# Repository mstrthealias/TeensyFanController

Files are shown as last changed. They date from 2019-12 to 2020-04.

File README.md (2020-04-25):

# Teensy Fan Controller

*Documentation: [https://mstrthealias.gitbook.io/teensy-fan-controller/][7]*

A PC fan controller with temperature sensor input, for **[Teensy](https://www.pjrc.com/teensy/index.html) 3.x** USB Development Board(s).

Supports up to 6 fans (4pin/PWM), and up to 5 temperature sensors. Each fan may individually operate in PID, temperature-percent table, or fixed-percent control modes. Configuration is saved onto the device, and software is not required other than to configure the controller.

## Documentation

The project is **documented using Gitbook**, and accessible at **[https://mstrthealias.gitbook.io/teensy-fan-controller/][7]**.

## Releases

- v0.1.0
  - [Firmware (Teensy 3.2, 3.5)](https://github.com/mstrthealias/TeensyFanController/releases/tag/v0.1.0)
  - [Configuration UI (Windows 10)](https://github.com/mstrthealias/TFC-ui/releases/tag/v0.1.0)

## Hardware

* [Prototype - Simple PCB][4]: requires PCB fabrication (gerber files provided) and through-hole soldering
* [Prototype - Breadboard][2]: breadboard example with a single fan/single sensor
* [Prototype - Hand-made (Schmart Board based)][3]: uses over-the-shelf components (OK for single fan/single sensor builds)

## Software

### Qt UI

[Teensy Fan Controller UI (Qt5)](https://github.com/mstrthealias/TFC-ui): provides a user interface to configure or monitor the fan controller (only needed for initial configuration).

### Linux Kernel module (hwmon)

[Fork of liquidtux](https://github.com/mstrthealias/liquidtux): Linux kernel module for reading temperatures and fan RPMs using *lm-sensors* or *psensor*.  Tested on Ubuntu 18.04.

## Simple 001 PCB

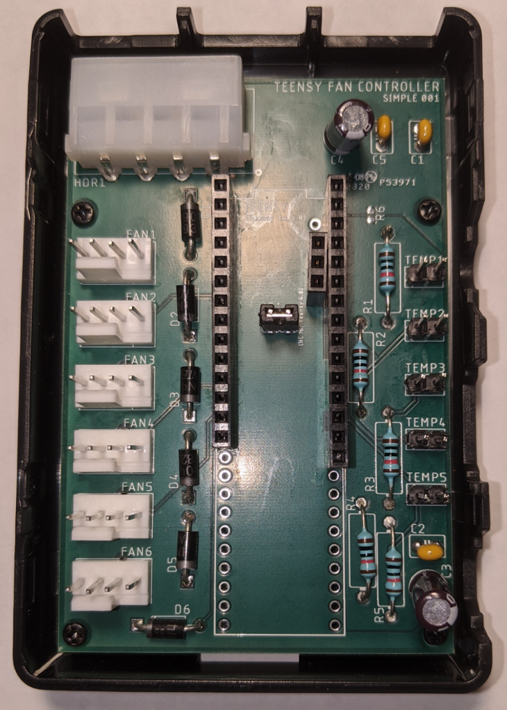
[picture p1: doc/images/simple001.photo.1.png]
Simple 001 PCB


## [Credits](https://mstrthealias.gitbook.io/teensy-fan-controller/credits)

Icons made by [Freepik](https://www.flaticon.com/authors/freepik) from [www.flaticon.com](https://www.flaticon.com/):

* ui_qt5/images/log.svg
* ui_qt5/images/worldwide.svg

[2]: https://mstrthealias.gitbook.io/teensy-fan-controller/hardware/breadboard
[3]: https://mstrthealias.gitbook.io/teensy-fan-controller/hardware/prototype
[4]: https://mstrthealias.gitbook.io/teensy-fan-controller/hardware/simple-pcb
[5]: Hardware/
[6]: https://mstrthealias.gitbook.io/teensy-fan-controller/demo/router-cooling-demo
[7]: https://mstrthealias.gitbook.io/teensy-fan-controller/

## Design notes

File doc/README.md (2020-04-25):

# Teensy Fan Controller

A PC fan controller with temperature sensor input, for **[Teensy](https://www.pjrc.com/teensy/index.html) 3.x** USB Development Board\(s\).

Supports up to 6 fans \(4pin/PWM\), and up to 5 temperature sensors \(thermistors\). Each fan may individually operate in PID, temperature-percent table, or fixed-percent control modes.

Designed to control radiator fans on a PC water cooling loop \(to maintain supply water temperature\), but may be configured for other purposes \(for example, see [Demo/Router Cooling Demo](demo/router-cooling-demo.md)\).

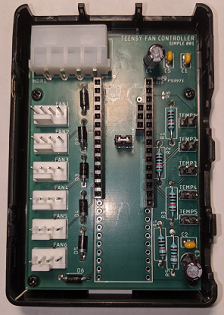
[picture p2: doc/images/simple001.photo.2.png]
Simple 001 PCB in a Raspberry Pi 3 case


## Releases

- v0.1.0
  - [Firmware (Teensy 3.2, 3.5)](https://github.com/mstrthealias/TeensyFanController/releases/tag/v0.1.0)
  - [Configuration UI (Windows 10)](https://github.com/mstrthealias/TFC-ui/releases/tag/v0.1.0)

## Hardware

The following hardware has been used with Teensy Fan Controller:

* [Prototype - Simple PCB](hardware/simple-pcb.md): requires PCB fabrication \(gerber files provided\) and through-hole soldering
* [Breadboard](hardware/breadboard.md): breadboard example with a single fan/single sensor
* [Prototype - Hand-made \(Schmart Board based\)](hardware/prototype.md): uses over-the-shelf components

Related files are available in the [TeensyFanController/Hardware](https://github.com/mstrthealias/TeensyFanController/tree/master/Hardware) folder.

### Hardware Interface

The Teensy Micro USB port is used to configure and monitor the fan controller.

{% hint style="info" %}
It is possible to connect the Micro USB port to an internal motherboard USB 1.1/2.0 header, by making a custom cable, or purchasing a _Micro USB 5pin Male to 1x 5Pin Female 0.1" USB Header PCB Motherboard Cable_.
{% endhint %}

## Software

### Qt UI

[Teensy Fan Controller UI \(Qt5\)](https://github.com/mstrthealias/TFC-ui): provides a user interface to configure or monitor the fan controller (only needed for initial configuration).

### Linux Kernel module \(hwmon\)

[Fork of liquidtux](https://github.com/mstrthealias/liquidtux): Linux kernel module for reading temperatures and fan RPMs using *lm-sensors* or *psensor*.  Tested on Ubuntu 18.04.

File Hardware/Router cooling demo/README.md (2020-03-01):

# Teensy Fan Controller - Router Cooling Demo

The controller is configured to cool a temperature sensor (placed between a desk router and switch) to a specific temperature.

A single PWM fan and single sensor is connected to a Teensy 3.2 using a breadboard.

## Hardware Requirements

1. One Breadboard, or a Teensy Fan Controller board (fe. Simple 001)
1. One Teensy 3.x with headers (previously *flashed with Teensy Fan Controller*)
1. A Micro USB cable
1. One 10k thermistor (fe. [Adafruit 10K Precision Epoxy Thermistor - 3950 NTC][1])
1. One 10k Ohm resistor (ideally 1% or better accuracy)
1. One standard/rectifier diode (fe. 1N4004)
1. One 12v power supply (up to 15V should be OK)
1. One PWM PC fan (80mm, 120mm, 140mm)
1. Wires

[1]: https://www.adafruit.com/product/372

## Hardware Setup

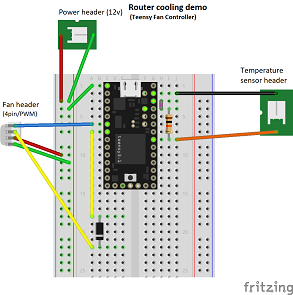
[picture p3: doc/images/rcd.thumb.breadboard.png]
Breadboard wiring diagram
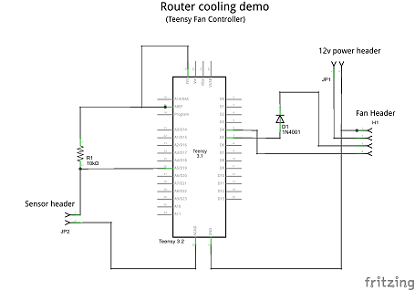
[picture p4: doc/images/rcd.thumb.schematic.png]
Schematic
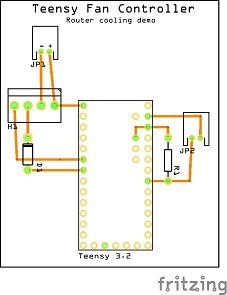
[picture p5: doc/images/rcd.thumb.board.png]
Board example
  

Steps to set up a breadboard with a Teensy 3.2, a single fan, a single temperature sensor, and a 12v power supply:

1. Place the **Teensy** into the top end of the breadboard (Teensy GND on breadboard row 1)
1. Place a **10k Ohm resistor** between **Teensy AREF** (breadboard **I4**) and **Teensy A5** (breadboard **I8**)
1. Place a **diode** with anode at **Teensy D5** (breadboard **A6**) and cathode at breadboard **row 22** (use a wire if needed)
1. Connect **Teensy GND** (breadboard **A1**) to the **GND bus** on the **left side** of the breadboard
1. Connect **Teensy AREF** (breadboard **H3**) to **Teensy V3.3** (breadboard **H4**)
1. Connect fan (4pin PWM):
   1. Connect **fan pin 1 (GND)** to the **GND bus** on the **left side** of the breadboard
   1. Connect **fan pin 2 (12V)** to the **PWR bus** on the **left side** of the breadboard
   1. Connect **fan pin 3 (RPM)** to breadboard **row 22** (cathode side of diode)
   1. Connect **fan pin 4 (PWM)** to **Teensy D4** (breadboard **A6**)
1. Connect thermistor:
   1. Connect **thermistor pin 1** to **Teensy A5** (breadboard **J8**)
   1. Connect **thermistor pin 2** to **Teensy AGND** (breadboard **J2**)
1. Connect 12v power supply the left breadboard bus:
   1. Connect **power supply GND** to the **GND bus** on the **left side** of the breadboard
   1. Connect **power supply +12V** to the **PWR bus** on the **left side** of the breadboard

### Sensor and fan placement

TODO 

<div class="ctbl-wrapper">
<table>
<tbody>
<tr>
<td>

* The temperature sensor is placed between the cases of a router stacked on top of a switch
* The fan is pointed at the router/switch

</td>
<td align="right">

Router cooling demo - sensor/fan setup

</td>
</tr>
</tbody>
</table>
</div>

## Software Setup

Note the Teensy connections made in the previous section:

Signal | Teensy Pin
------ | ---------
Fan 1 RPM pin | D5 (pin 5)
Fan 1 PWM pin | D4 (pin 4)
Thermistor pin 1 | A5 (pin 19)

Configure the software using the information given above:

<div class="ctbl-wrapper">
<table>
<tbody>
<tr>
<td>

1. Connect the **Micro USB cable** to the **Teensy 3.x**
1. Launch **Teensy Fan Controller UI**
1. Select **Menu** > **Hardware Setup**
1. Enter the following:

    Field | Value
    ----- | -----:
    Water Supply Temp Sensor: Pin | **19**
    Water Return Temp Sensor: Pin | 0
    Case Temp Sensor: Pin | 0
    Aux1 Temp Sensor: Pin | 0
    Aux2 Temp Sensor: Pin | 0
    Fan 1: PWM Pin | **4**
    Fan 1: RPM Pin | **5**
    Fan 2: PWM Pin | 0
    Fan 2: RPM Pin | 0
    Fan 3: PWM Pin | 0
    Fan 3: RPM Pin | 0
    Fan 4: PWM Pin | 0
    Fan 4: RPM Pin | 0
    Fan 5: PWM Pin | 0
    Fan 5: RPM Pin | 0
    Fan 6: PWM Pin | 0
    Fan 6: RPM Pin | 0

1. Click **Save**
1. Click the **back arrow** on the top-left

</td>
<td align="right">

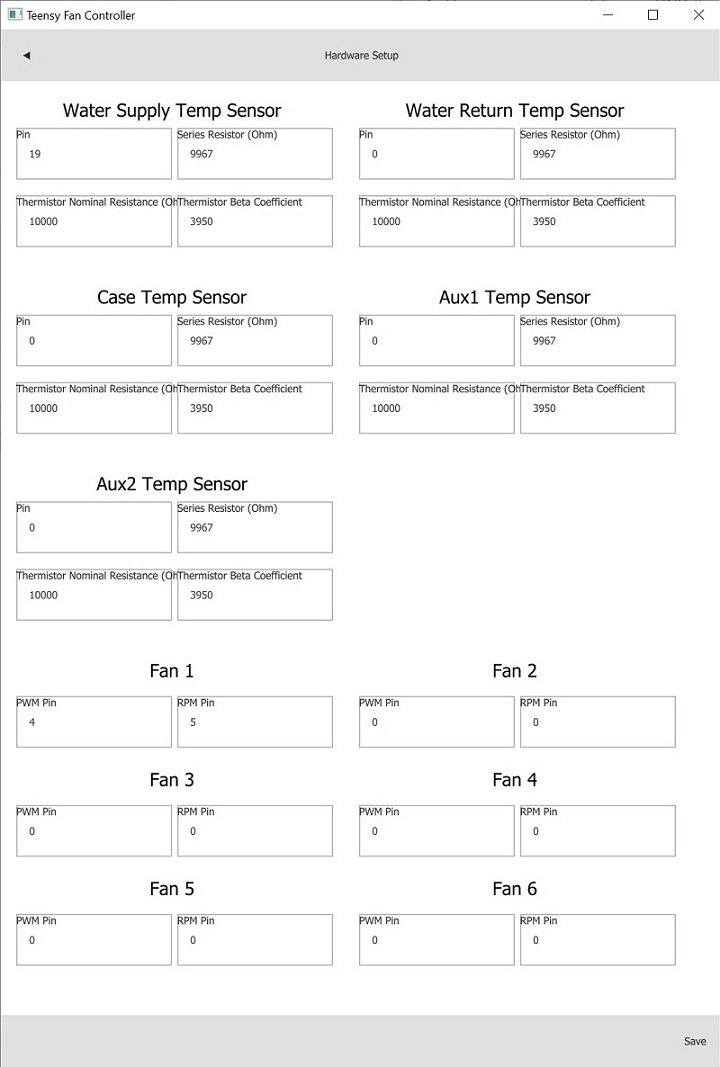
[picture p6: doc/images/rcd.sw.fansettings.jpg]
Router cooling demo - fan settings


</td>
</tr>
</tbody>
</table>
</div>

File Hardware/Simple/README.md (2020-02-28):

# Teensy Fan Controller - PCB Simple001

The initial, untested, simple Teensy Fan Controller PCB.

Designed to fit in a [Raspberry Pi 3 case][1].

## Instructions

TODO

## Notes

After this revision has been tested, a 2nd revision--Simple002--will be published, possibly removing features such as the AGND-GND bridge and V3.3-AREF jumper.

- The jumper in the middle ties v3.3 to ADC reference voltage

TODO

## Features

TODO

- Supports Teensy 3.x, and Teensy 4.0
- Standard 4pin Molex PC power connector
- Fits in a [Raspberry Pi 3 case][1]
- 6 fans
- 5 temperature sensors

## Paths

| Path | Description |
|---|---|
| [datasheets/][2] | Part datasheets
| [simple001/EAGLE/][3] | EAGLE library, schematic, and board (Simple001)
| [simple001/gerbers.zip][4] | Gerber files for PCB fabrication (Simple001)
| [simple001/parts.csv][5] | Part order list (Simple001)
| [simple001/partslist.txt][6] | Modified EAGLE partlist.txt export (Simple001)
| [simple001/schematic.pdf][7] | Schematic print-out PDF (Simple001)
| [simple001/freeDFM.pdf][8] | freeDFM multi-layer PDF output results (Simple001)

[1]: https://www.microcenter.com/product/614861/micro-connectors-plastic-raspberry-pi-3-model-b-case-kit
[2]: datasheets/
[3]: simple001/EAGLE/
[4]: simple001/gerbers.zip
[5]: simple001/parts.csv
[6]: simple001/partslist.txt
[7]: simple001/schematic.pdf
[8]: simple001/freeDFM.pdf

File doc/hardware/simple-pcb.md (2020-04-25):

# Simple PCB

The initial Teensy Fan Controller PCB, designed to fit in a [Raspberry Pi 3 case](https://www.microcenter.com/product/614861/micro-connectors-plastic-raspberry-pi-3-model-b-case-kit):

Simple 001 PCB in a Raspberry Pi 3 case

{% hint style="info" %}
[Simple002 design files](https://github.com/mstrthealias/TeensyFanController/blob/master/Hardware/Simple/simple002) are available, but untested.
{% endhint %}

## Build Instructions

* Order PCB fabrication using the provided [Gerber files](https://github.com/mstrthealias/TeensyFanController/blob/master/Hardware/Simple/simple001/gerbers.zip) \(fe. 4pcb 33each\)
* Order parts using provided [bill-of-materials](https://github.com/mstrthealias/TeensyFanController/blob/master/Hardware/Simple/simple001/parts.csv)
* Solder parts onto PCB, guided by the provided [parts list](https://github.com/mstrthealias/TeensyFanController/blob/master/Hardware/Simple/simple001/partslist.txt)

{% hint style="info" %}
_Simple 001_ board mount holes do not exactly fit the enclosure. Perform these steps to fit the PCB in the enclosure:

* Increase board mount hole size using a _7/64"_ drill bit
* Remove the in-board portion of the enclosure stand-offs \(keeping the majority of each stand-off\)
{% endhint %}

## Features

* Supports Teensy 3.x
* Standard 4pin Molex PC power connector
* Fits in a [Raspberry Pi 3 case](https://www.microcenter.com/product/614861/micro-connectors-plastic-raspberry-pi-3-model-b-case-kit)
* 6 fans
* 5 temperature sensors

{% hint style="warning" %}
_Simple 001_ **fan 6** control is not functional when used with a Teensy 3.2.
{% endhint %}

## Notes

* The jumper in the middle \(JP1\) ties v3.3 to ADC reference voltage
* The AGND-GND bridge \(R6\) is left open

{% hint style="info" %}
A 2nd revision--Simple002--will be published, removing the AGND-GND bridge and the V3.3-AREF jumper.
{% endhint %}

## Paths

| Path | Description |
| :--- | :--- |
| [datasheets/](https://github.com/mstrthealias/TeensyFanController/tree/master/Hardware/Simple/datasheets) | Part datasheets |
| [EAGLE/](https://github.com/mstrthealias/TeensyFanController/tree/master/Hardware/Simple/EAGLE) | EAGLE library, schematic, and board \(_Simple 002_\) |
| [simple001/gerbers.zip](https://github.com/mstrthealias/TeensyFanController/tree/0ceefdbffbd5efc627939be4be3313a873193821/Hardware/Simple/simple001/gerbers.zip) | Gerber files for PCB fabrication \(_Simple 001_\) |
| [simple001/parts.csv](https://github.com/mstrthealias/TeensyFanController/tree/0ceefdbffbd5efc627939be4be3313a873193821/Hardware/Simple/simple001/parts.csv) | Part order list \(_Simple 001_\) |
| [simple001/partslist.txt](https://github.com/mstrthealias/TeensyFanController/tree/0ceefdbffbd5efc627939be4be3313a873193821/Hardware/Simple/simple001/partslist.txt) | Modified EAGLE partlist.txt export \(_Simple 001_\) |
| [simple001/schematic.pdf](https://github.com/mstrthealias/TeensyFanController/tree/0ceefdbffbd5efc627939be4be3313a873193821/Hardware/Simple/simple001/schematic.pdf) | Schematic print-out PDF \(_Simple 001_\) |
| [simple001/freeDFM.pdf](https://github.com/mstrthealias/TeensyFanController/tree/0ceefdbffbd5efc627939be4be3313a873193821/Hardware/Simple/simple001/freeDFM.pdf) | freeDFM multi-layer PDF output results \(_Simple 001_\) |

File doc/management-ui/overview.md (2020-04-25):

# Overview

A Qt 5 based application to configure or monitor a Teensy Fan Controller.

{% hint style="info" %}
After clicking Save, the configuration is saved onto the hardware, and is restored after power-loss \(without using the _Management UI_\).
{% endhint %}

## Getting Started

The application attempts to connect when launched:

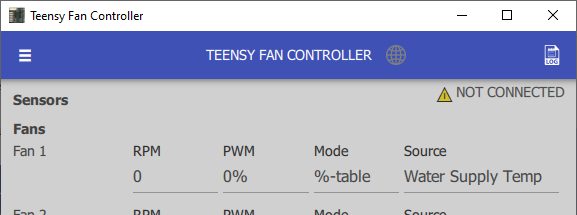
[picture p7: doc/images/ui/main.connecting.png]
Management UI - Home screen (connecting)


Once connected, the active configuration is downloaded:

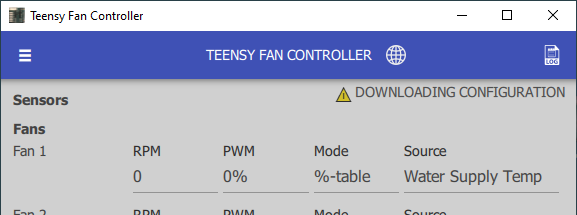
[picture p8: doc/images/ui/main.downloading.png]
Management UI - Home screen (downloading configuration)


Once downloaded, the present values are displayed:

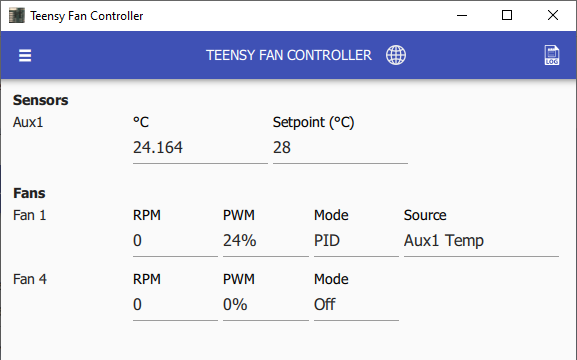
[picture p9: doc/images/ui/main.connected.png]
Management UI - Home screen (connected)


## Usage

Clicking the **menu button** provides access to 3 pages:

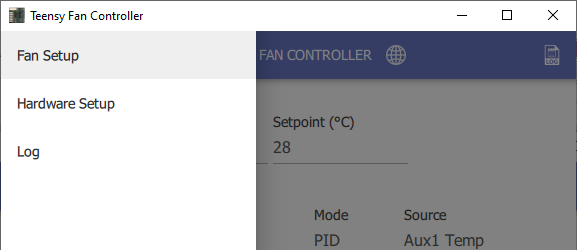
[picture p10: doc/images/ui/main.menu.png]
Management UI - Main menu


The **log window** may also be opened by clicking the **LOG button** on the top right:

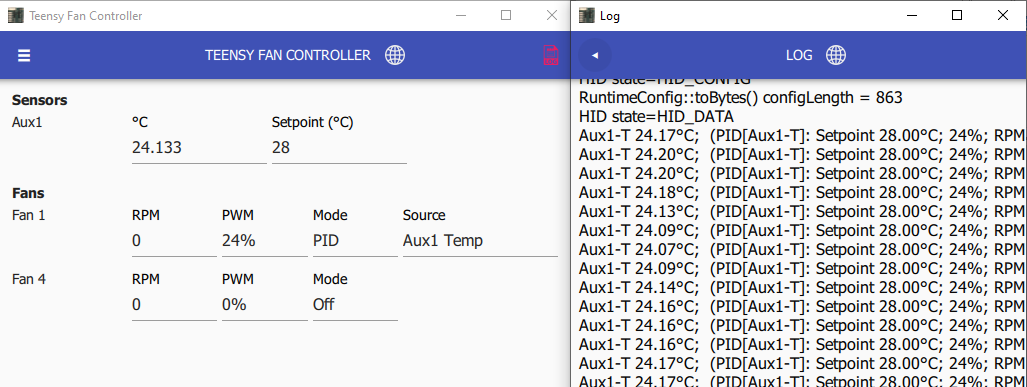
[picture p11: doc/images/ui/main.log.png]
Management UI - Log screen


If the application fails to connect, or losses connection, the red globe icon in the toolbar may be clicked to reconnect:

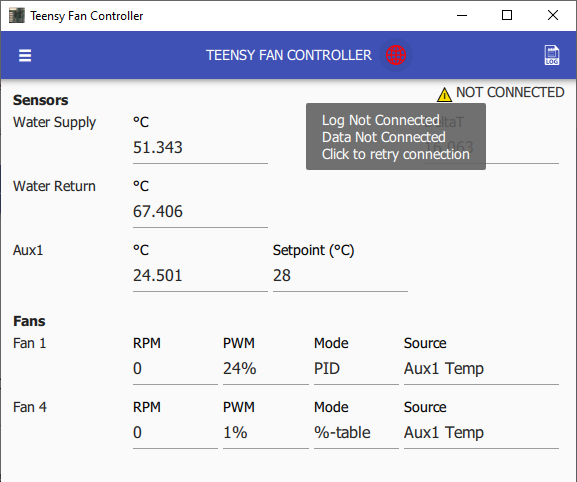
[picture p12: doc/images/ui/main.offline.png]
Management UI - Home screen - Offline


### Pages

| Page | Description |
| :--- | :--- |
| Controller Status (Home) | Display current fan RPMs and temperature readings \(updates every 500 ms\) |
| Hardware Setup | Sensor and fan hardware configuration \(fe. pin mapping, thermistor resistance, etc.\) |
| Fan Setup | Fan speed configuration \(fe. control mode, temperature sensor source, etc.\) |
| Controller Log | Debug logs sent from controller \(values printed every 5 seconds\) |

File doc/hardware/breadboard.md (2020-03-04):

# Breadboard

A single PWM fan and single sensor is connected to a Teensy 3.2 using a breadboard.

## Hardware Requirements

1. One Breadboard
2. One Teensy 3.x with headers \(previously _flashed with Teensy Fan Controller_\)
3. A Micro USB cable
4. One 10k thermistor \(fe. [Adafruit 10K Precision Epoxy Thermistor - 3950 NTC](https://www.adafruit.com/product/372)\)
5. One 10k Ohm resistor \(ideally 1% or better accuracy\)
6. One standard/rectifier diode \(fe. 1N4004\)
7. One 12v power supply \(up to 15V should be OK\)
8. One PWM PC fan \(80mm, 120mm, 140mm\)
9. Wires

## Hardware Setup

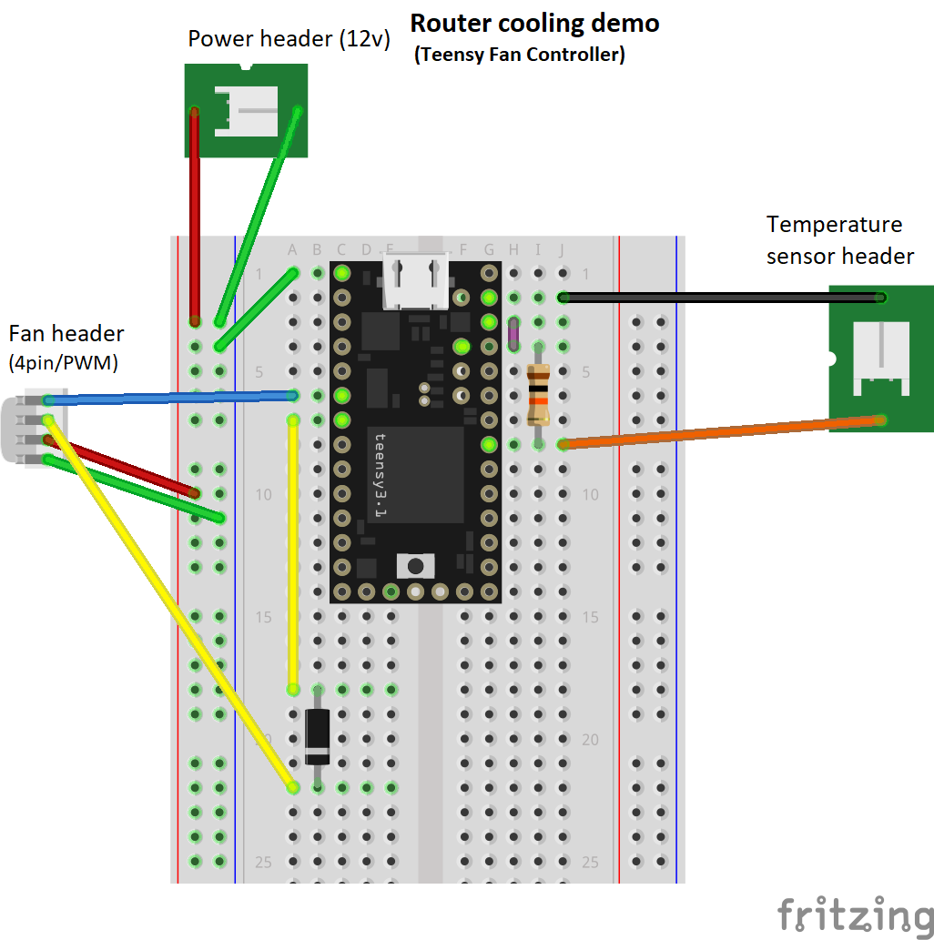
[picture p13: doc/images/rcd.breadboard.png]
Breadboard wiring diagram
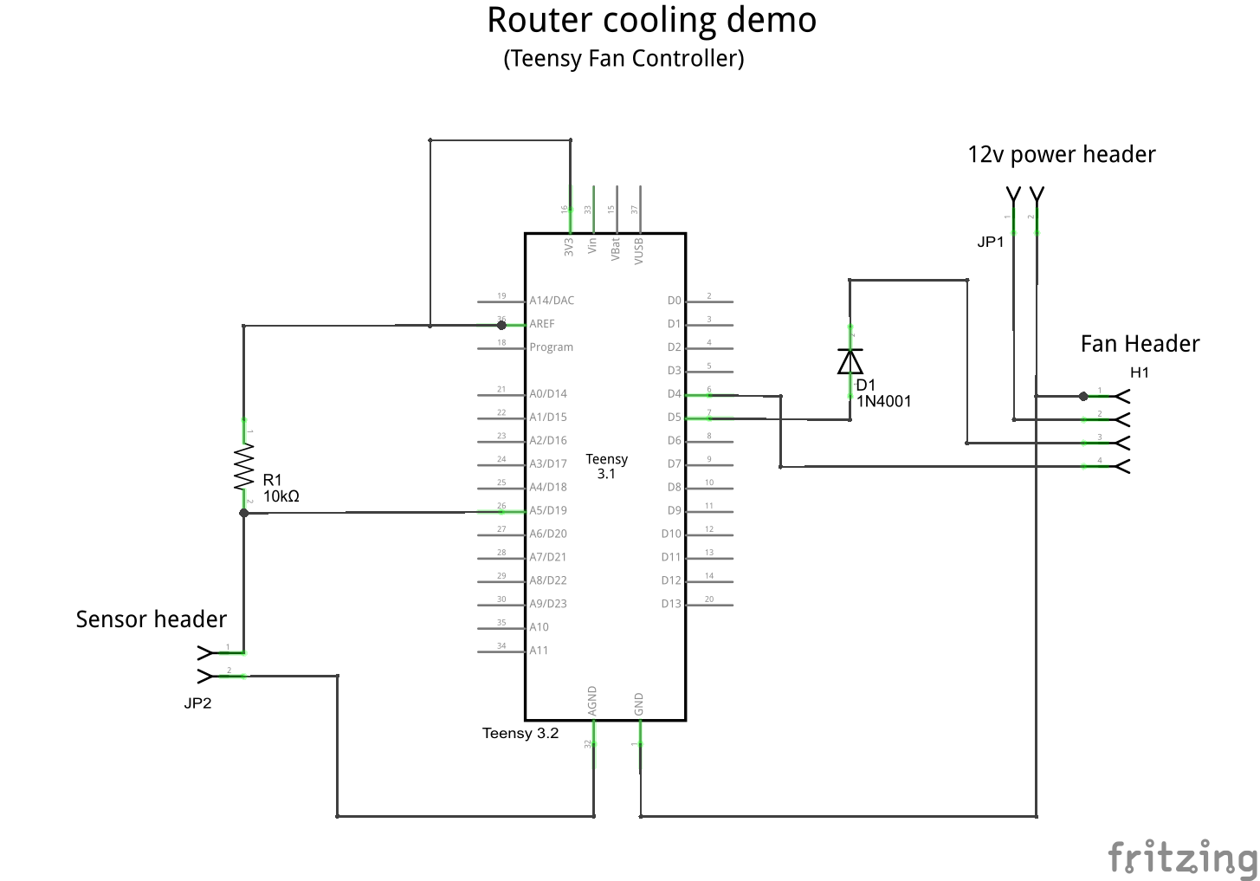
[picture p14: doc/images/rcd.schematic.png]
Schematic
 

Steps to set up a breadboard with a Teensy 3.2, a single fan, a single temperature sensor, and a 12v power supply:

1. Place the **Teensy** into the top end of the breadboard \(**Teensy GND** on breadboard **row 1**\)
2. Place a **10k Ohm resistor** between **Teensy AREF** \(breadboard **I4**\) and **Teensy A5** \(breadboard **I8**\)
3. Place a **diode** with anode at **Teensy D5** \(breadboard **A6**\) and cathode at breadboard **row 22** \(use a wire if needed\)
4. Connect **Teensy GND** \(breadboard **A1**\) to the **GND bus** on the **left side** of the breadboard
5. Connect **Teensy AREF** \(breadboard **H3**\) to **Teensy V3.3** \(breadboard **H4**\)
6. Connect fan \(4pin PWM\):
   1. Connect **fan pin 1 \(GND\)** to the **GND bus** on the **left side** of the breadboard
   2. Connect **fan pin 2 \(12V\)** to the **PWR bus** on the **left side** of the breadboard
   3. Connect **fan pin 3 \(RPM\)** to breadboard **row 22** \(cathode side of diode\)
   4. Connect **fan pin 4 \(PWM\)** to **Teensy D4** \(breadboard **A6**\)
7. Connect thermistor:
   1. Connect **thermistor pin 1** to **Teensy A5** \(breadboard **J8**\)
   2. Connect **thermistor pin 2** to **Teensy AGND** \(breadboard **J2**\)
8. Connect 12v power supply the left breadboard bus:
   1. Connect **power supply GND** to the **GND bus** on the **left side** of the breadboard
   2. Connect **power supply +12V** to the **PWR bus** on the **left side** of the breadboard

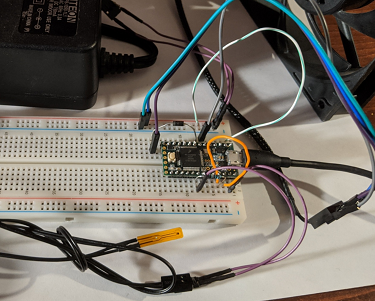
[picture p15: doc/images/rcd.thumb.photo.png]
Breadboard example
 Board example

## Software Setup

Note the Teensy connections made in the previous section:

| Signal | Teensy Pin |
| :--- | :--- |
| Fan 1 RPM pin | D5 \(pin 5\) |
| Fan 1 PWM pin | D4 \(pin 4\) |
| Thermistor pin 1 | A5 \(pin 19\) |

Configure the software using the information given above:

1. Connect the **Micro USB cable** to the **Teensy 3.x**
2. Launch **Teensy Fan Controller UI**
3. Select **Menu** &gt; **Hardware Setup**
4. Enter the following:

   | Field | Value |
   | :--- | ---: |
   | Water Supply Temp Sensor: Pin | **19** |
   | Water Return Temp Sensor: Pin | 0 |
   | Case Temp Sensor: Pin | 0 |
   | Aux1 Temp Sensor: Pin | 0 |
   | Aux2 Temp Sensor: Pin | 0 |
   | Fan 1: PWM Pin | **4** |
   | Fan 1: RPM Pin | **5** |
   | Fan 2: PWM Pin | 0 |
   | Fan 2: RPM Pin | 0 |
   | Fan 3: PWM Pin | 0 |
   | Fan 3: RPM Pin | 0 |
   | Fan 4: PWM Pin | 0 |
   | Fan 4: RPM Pin | 0 |
   | Fan 5: PWM Pin | 0 |
   | Fan 5: RPM Pin | 0 |
   | Fan 6: PWM Pin | 0 |
   | Fan 6: RPM Pin | 0 |

5. Click **Save**

{% hint style="info" %}
After making changes, the Hardware Setup screen should appear as:

Breadboard - fan settings
{% endhint %}

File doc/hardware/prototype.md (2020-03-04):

# Prototype

Schmart Board based Teensy Fan Controller prototype v1:

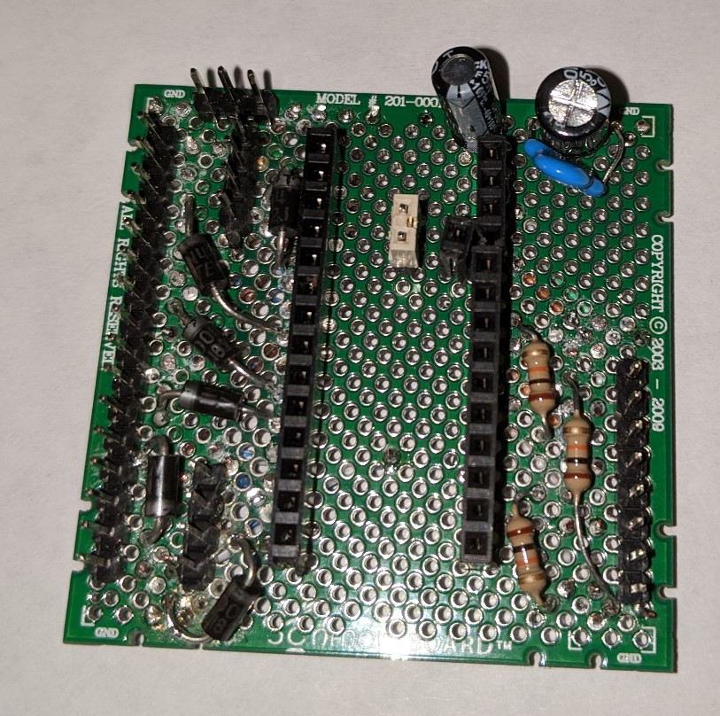
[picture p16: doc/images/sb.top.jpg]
Schmart Board based prototype - top
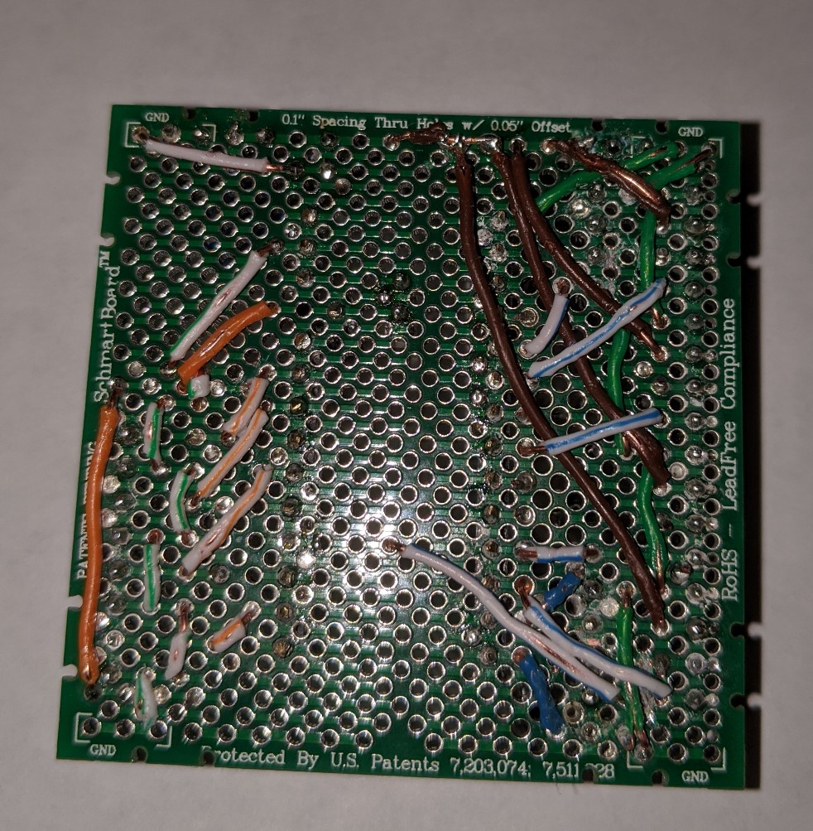
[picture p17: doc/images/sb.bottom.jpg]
Schmart Board based prototype - bottom
 

Design files available at: [Hardware/Schmart Board](https://github.com/mstrthealias/TeensyFanController/tree/master/Hardware/Schmart%20Board)

## Notes

* 1% accuracy resistors should be used, though resistances are configurable to calibrate readings
* The jumper in the middle ties v3.3 to ADC reference voltage
* The capacitors are not described in the prototype layout
* Only 3 of the 4 sensor resistors are soldered in the images
* The 4 fan headers in a row should be split in the middle, or possibly re-arranged in a 3 x 2 configuration

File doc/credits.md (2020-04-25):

# Credits

## Authors

* [Jack Davis](https://github.com/mstrthealias)

## Design

- https://electronics.stackexchange.com/a/214082

## Icons

Icons made by [Freepik](https://www.flaticon.com/authors/freepik) from [www.flaticon.com](https://www.flaticon.com/):

* [ui_qt5/images/log.svg](https://github.com/mstrthealias/TFC-ui/blob/master/images/log.svg)
* [ui_qt5/images/worldwide.svg](https://github.com/mstrthealias/TFC-ui/blob/master/images/worldwide.svg)

## Code

- https://github.com/br3ttb/Arduino-PID-Library/ (License MIT)
- https://learn.adafruit.com/thermistor/using-a-thermistor (License Apache?)
- https://stackoverflow.com/a/10990893/1345237 (License ?)
- https://github.com/apmorton/teensy-template (License ?)

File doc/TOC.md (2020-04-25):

# Table of contents

* [Teensy Fan Controller](README.md)

## Usage

* [Fan Control](usage/fan-control-modes.md)

## Hardware

* [Simple PCB](hardware/simple-pcb.md)
* [Breadboard](hardware/breadboard.md)
* [Prototype](hardware/prototype.md)

## Management UI

* [Overview](management-ui/overview.md)
* [Controller Status](management-ui/present-values.md)
* [Hardware Setup](management-ui/hardware-setup.md)
* [Fan Setup](management-ui/fan-setup.md)
* [Controller Log](management-ui/controller-log.md)

## Build Instructions

* [Project Setup](build-instructions/setup.md)
* [Firmware \(Teensy\)](build-instructions/firmware.md)
* [Management UI](build-instructions/ui.md)

## Demo

* [Router Cooling Demo](demo/router-cooling-demo.md)
* [Water-cooled CPU and air-cooled GPU](demo/pc-water-cooling-demo-1.md)

## Credits

* [Credits](credits.md)

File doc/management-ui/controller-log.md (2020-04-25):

# Controller Log

Displays debug log messages sent from the controller.

{% hint style="info" %}
An entry is printed every 5 seconds, or after user interaction from the Management UI.
{% endhint %}

TODO

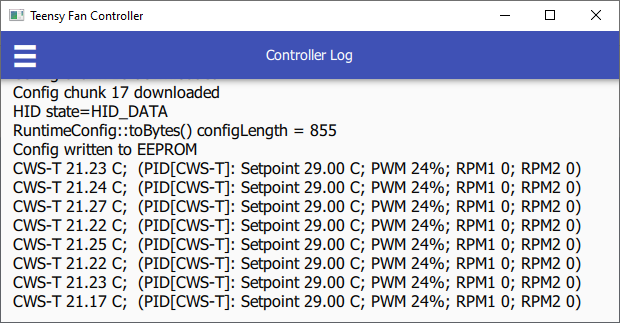
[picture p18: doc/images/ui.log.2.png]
Controller Log screenshot


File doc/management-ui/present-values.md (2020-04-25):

# Controller Status (Home Screen)

Displays present temperatures, present fan speeds, and active fan configurations.

{% hint style="info" %}
Disabled fans or sensors (**pin set to 0**) will be hidden from this view.
{% endhint %}

{% hint style="info" %}
Fan RPMs and temperature readings may be monitored using the [liquidtux Linux hwmon module](https://github.com/mstrthealias/liquidtux) \(a Windows equivalent will be available later\).
{% endhint %}

TODO

Management UI - Home screen

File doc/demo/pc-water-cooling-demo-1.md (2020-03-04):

# Water-cooled CPU and air-cooled GPU

TODO

## PID Usage and Example

TODO

The default configuration works well on a PC with a water-cooled CPU and an air-cooled GPU:

* Uses a supply water temperature sensor and a case temperature sensor
* Controls supply water temperature to 2-3°C above case temperature \(initial setpoint is 28°C\)
* Fan output percent is generally between 45%-60%, unless CPU is loaded
* If case temperature is within 2°C of supply water temperature, and fan output percent is greater than 60% for 20 seconds, the setpoint increases by 0.25°C

For example, the fans are controlled to keep supply water temperature at setpoint:

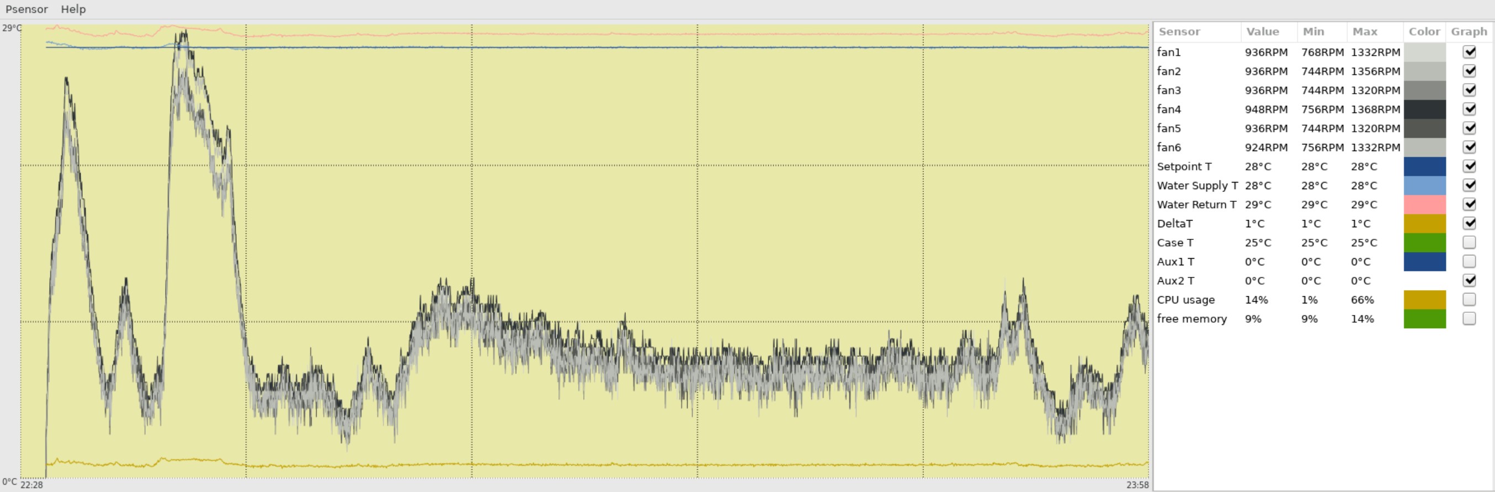
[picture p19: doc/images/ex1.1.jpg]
Example 1.1


In the same dataset as _Example 1.1_, and only plotting fan RPMs and DeltaT \(return temp - supply temp\), observe the fan speeds trailing DeltaT \(which represents CPU load in the following example\):

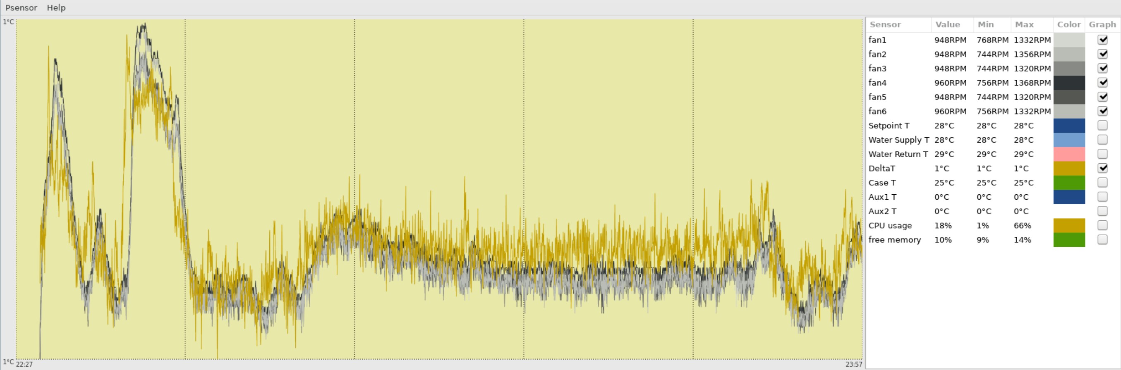
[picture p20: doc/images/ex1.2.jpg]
Example 1.2


Next, an air-cooled GPU is used for about 30 minutes, showing _setpoint adjustment_ keeping fan speeds within the configured range:

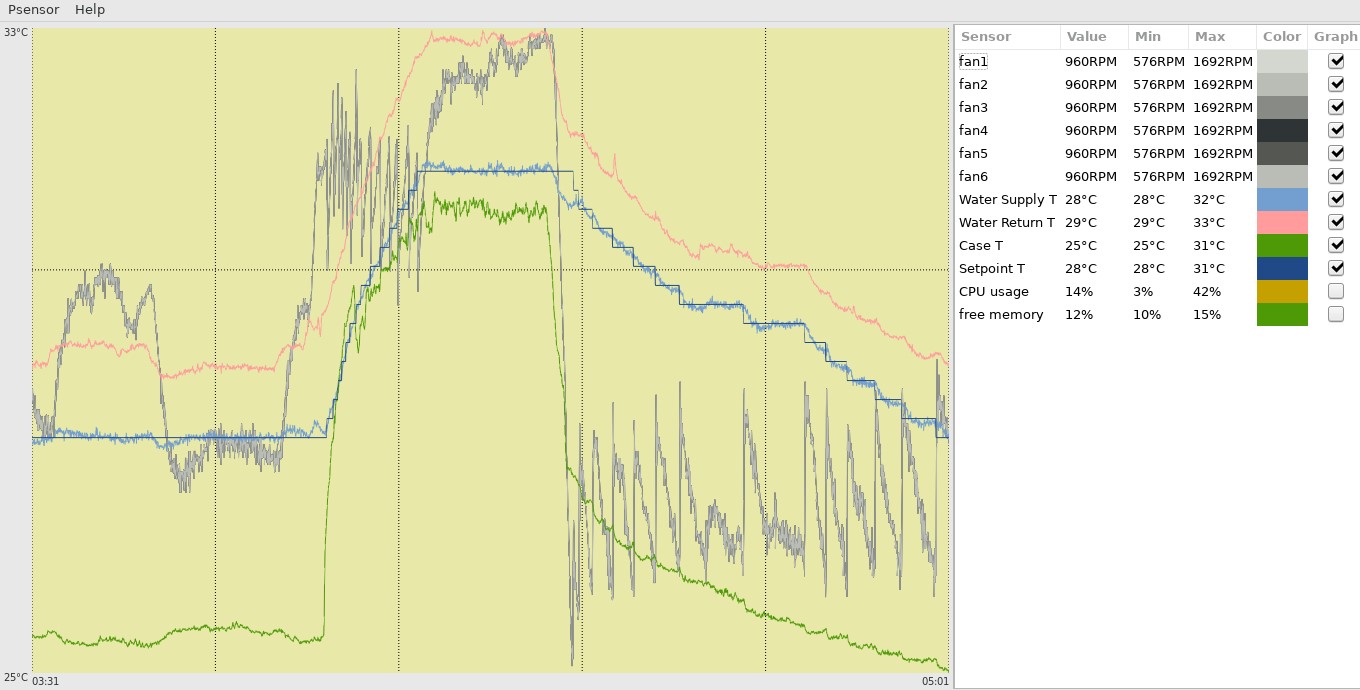
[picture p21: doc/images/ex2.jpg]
Example 2


The same behavior is observed, except caused by room temperature changes, in this example:

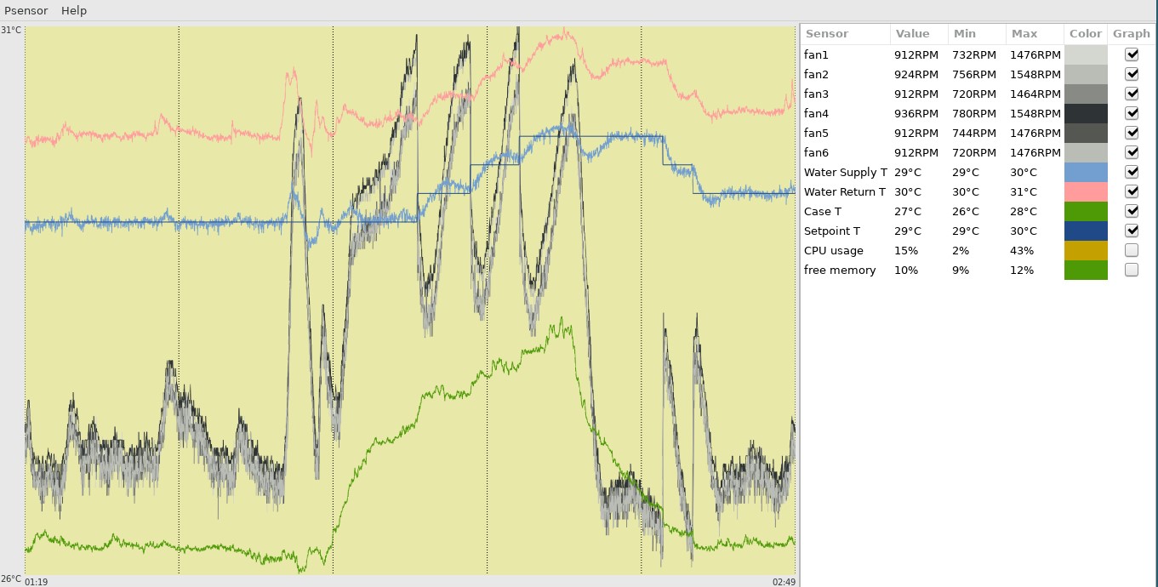
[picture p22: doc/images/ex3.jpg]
Example 3


When only the CPU is loaded, the setpoint temperature does not change, and the fans speed up as needed:

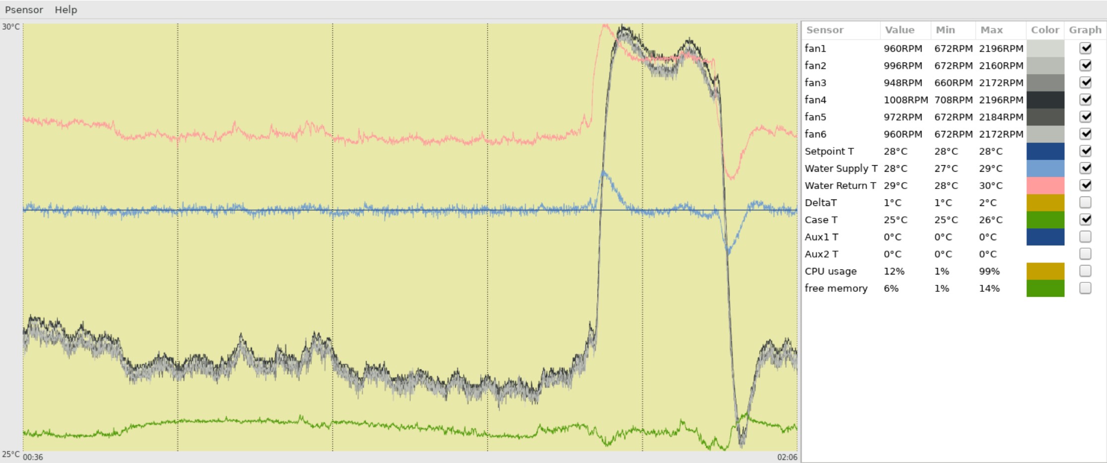
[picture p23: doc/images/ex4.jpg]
Example 4


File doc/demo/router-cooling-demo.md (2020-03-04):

# Router Cooling Demo

The controller is configured to cool a temperature sensor \(placed between a desk router and switch\) to a specific temperature.

## Hardware Requirements

1. A Teensy Fan Controller \(fe. [Breadboard](../hardware/breadboard.md), [Schmart Board prototype](../hardware/prototype.md), [Simple PCB](../hardware/simple-pcb.md)\)
2. One Teensy 3.x with headers \(previously _flashed with Teensy Fan Controller_\)
3. A Micro USB cable
4. One 12v power supply \(up to 15V should be OK\)
5. One PWM PC fan \(80mm, 120mm, 140mm\)
6. Wires

## Sensor and fan placement

* The temperature sensor is placed between the cases of a router stacked on top of a switch
* The fan is pointed at the router/switch

TODO

Router cooling demo - sensor/fan setup

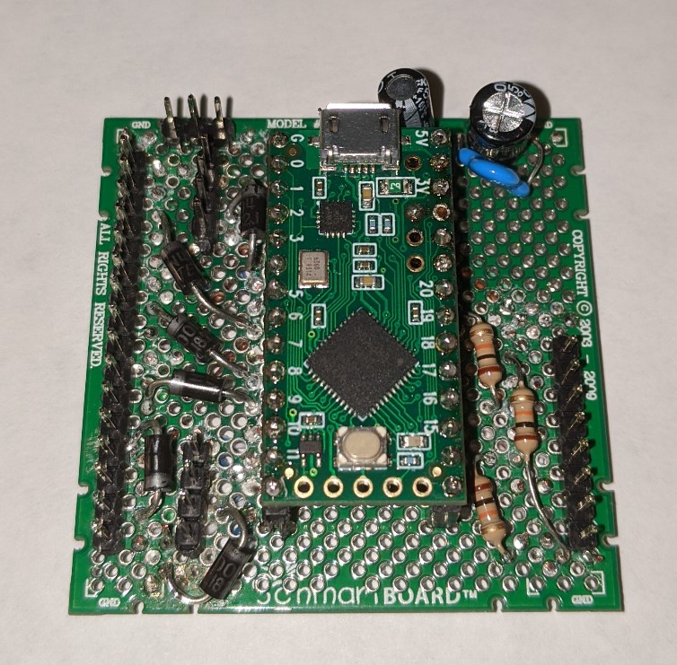
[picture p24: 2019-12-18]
Hardware/Schmart Board/Top with TeensyLC.jpg

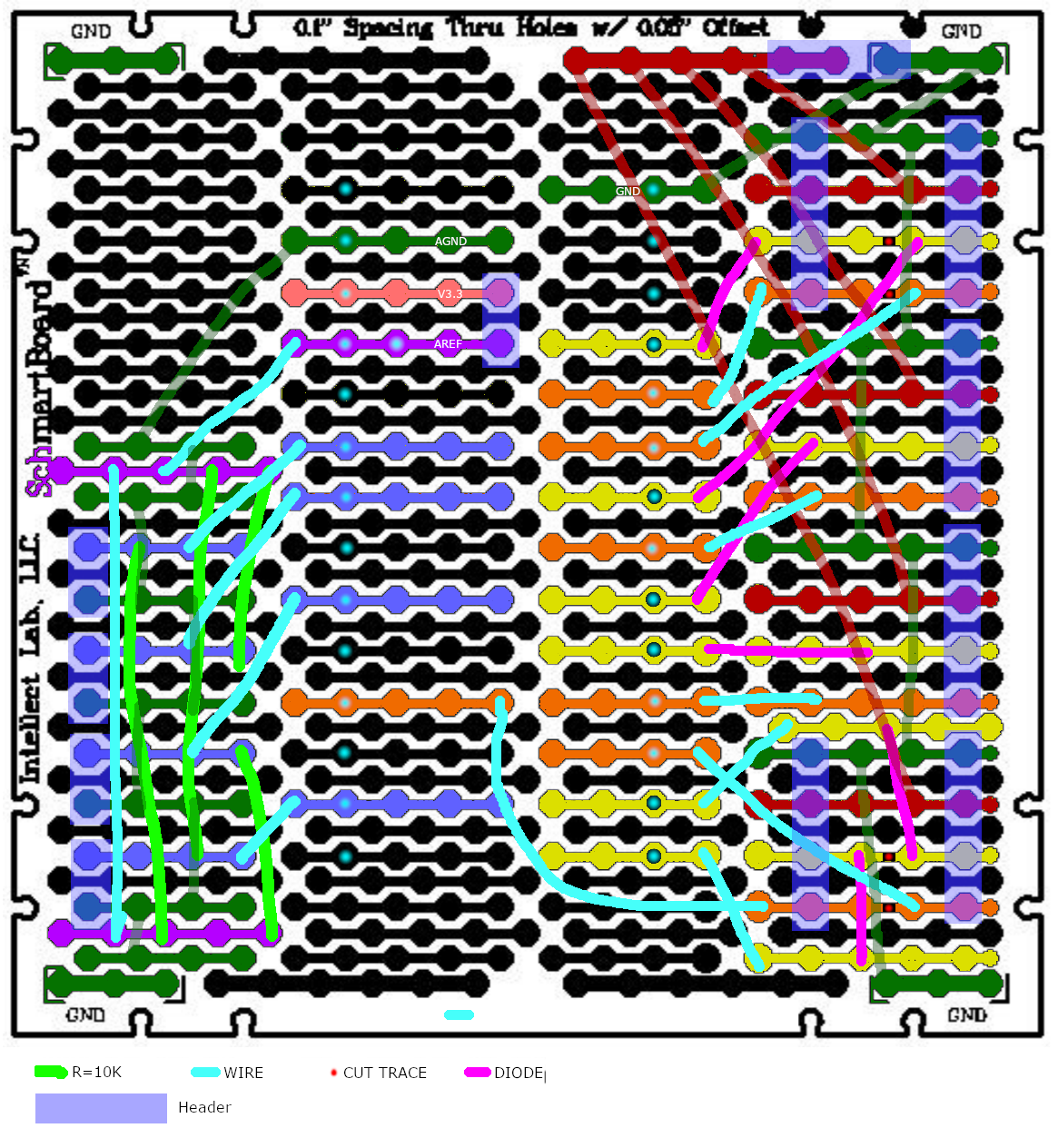
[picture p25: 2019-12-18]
Hardware/Schmart Board/layout.png

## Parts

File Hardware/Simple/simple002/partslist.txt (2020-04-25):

Qty Value            Device           Package          Parts                  Description                                               BUILT_BY    CREATED_BY    DESC                            DIGIKEY_PART_NUMBER MANUFACTURER              MANUFACTURER_PART_NUMBER PACKAGE POPULARITY SPICEPREFIX
3   0.1uF            C2,5-3           C2.5-3           C1, C2, C5             CAPACITOR                                                                           CAP CER 0.1UF 100V Z5U RADIAL   399-14023-1-ND      KEMET                     C320C104M1U5TA7303               38                    
5   10K              R-US_V234/12     V234/12          R1, R2, R3, R4, R5     RESISTOR, American symbol                                                           RES 10K OHM 1/4W 1% AXIAL       RNF14FTD10K0CT-ND   Stackpole Electronics Inc RNF14FTD10K0                                           
1   10uF             CPOL-USE2.5-5    E2,5-5           C3                     POLARIZED CAPACITOR, American symbol                                                CAP ALUM 10UF 20% 50V THRU HOLE 493-16250-1-ND      Nichicon                  ULD1H100MDD1TD                   8          C          
1   10uF             CPOL-USE2.5-5    E2,5-5           C4                     POLARIZED CAPACITOR, American symbol                                                CAP ALUM 10UF 20% 50V THRU HOLE 493-16250-1-ND      Nichicon                  ULD1H100MDD1TD                                         
6   1N4934           1N4934           DO-41            D1, D2, D3, D4, D5, D6 DIODE GEN PURP 400V 1A DO41                                           PCBLayout.com DIODE GEN PURP 100V 1A DO41     1N4934DICT-ND       Diodes Incorporated       1N4934-T                 DO-41                         
1   FAN1             HDR-FAN4         FAN4             FAN1                   PIN HEADER                                                                          CONN HEADER VERT 4POS 2.54MM    WM4330-ND           Molex                     0470531000                                             
1   FAN2             HDR-FAN4         FAN4             FAN2                   PIN HEADER                                                                          CONN HEADER VERT 4POS 2.54MM    WM4330-ND           Molex                     0470531000                                             
1   FAN3             HDR-FAN4         FAN4             FAN3                   PIN HEADER                                                                          CONN HEADER VERT 4POS 2.54MM    WM4330-ND           Molex                     0470531000                                             
1   FAN4             HDR-FAN4         FAN4             FAN4                   PIN HEADER                                                                          CONN HEADER VERT 4POS 2.54MM    WM4330-ND           Molex                     0470531000                                             
1   FAN5             HDR-FAN4         FAN4             FAN5                   PIN HEADER                                                                          CONN HEADER VERT 4POS 2.54MM    WM4330-ND           Molex                     0470531000                                             
1   FAN6             HDR-FAN4         FAN4             FAN6                   PIN HEADER                                                                          CONN HEADER VERT 4POS 2.54MM    WM4330-ND           Molex                     0470531000                                             
1   JMP              R-US_R0402       R0402            R6                     RESISTOR, American symbol                                                           UNUSED                                                                                                                               
1   PWRHDR           641737-1         641737-1         HDR1                                                                             EMA_UL_Team               CONN HEADER R/A 4POS 5.08MM     A25430-ND           TE Connectivity           641737-1                                               
1   TEENSY_3.5_DIL+4 TEENSY_3.5_DIL+4 TEENSY_3.5_DIL+4 TEENSY                 DIL version of Teensy 3.5 plus the VUSB/A10/A11/AREF PINS                           TEENSY 3.5 W/ HDRS K64 EVAL BRD 1568-1464-ND        SparkFun Electronics      DEV-14056                                              
1   TEENSY_3.5_DIL+4 TEENSY_3.5_DIL+4 TEENSY_3.5_DIL+4 TEENSY                 CONN HDR 14POS 0.1 TIN PCB                                                          CONN HDR 14POS 0.1 TIN PCB      S7012-ND            Sullins Connector Solutio PPTC141LFBN-RC                                         
1   TEENSY_3.5_DIL+4 TEENSY_3.5_DIL+4 TEENSY_3.5_DIL+4 TEENSY                 CONN HDR 15POS 0.1 TIN PCB                                                          CONN HDR 15POS 0.1 TIN PCB      S7013-ND            Sullins Connector Solutio PPTC151LFBN-RC                                         
1   TEENSY_3.5_DIL+4 TEENSY_3.5_DIL+4 TEENSY_3.5_DIL+4 TEENSY                 CONN HDR 3POS 0.1 GOLD PCB                                                          CONN HDR 3POS 0.1 GOLD PCB      S7036-ND            Sullins Connector Solutio PPPC031LFBN-RC                                         
1   TEMP1            HDR-SENSOR2      SENSOR2          TEMP1                  PIN HEADER                                                                          Break Away Headers - Straight   PRT-00116           SparkFun Electronics      PRT-00116                                              
1   TEMP2            HDR-SENSOR2      SENSOR2          TEMP2                  PIN HEADER                                                                          Break Away Headers - Straight   PRT-00116           SparkFun Electronics      PRT-00116                                              
1   TEMP3            HDR-SENSOR2      SENSOR2          TEMP3                  PIN HEADER                                                                          Break Away Headers - Straight   PRT-00116           SparkFun Electronics      PRT-00116                                              
1   TEMP4            HDR-SENSOR2      SENSOR2          TEMP4                  PIN HEADER                                                                          Break Away Headers - Straight   PRT-00116           SparkFun Electronics      PRT-00116                                              
1   TEMP5            HDR-SENSOR2      SENSOR2          TEMP5                  PIN HEADER                                                                          Break Away Headers - Straight   PRT-00116           SparkFun Electronics      PRT-00116

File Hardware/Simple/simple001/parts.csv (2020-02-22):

Description | Cost | Quantity | Total | URL
Break Away Headers - Straight | 1.5 | 2 | 3 | https://www.sparkfun.com/products/116
PWRHDR: CONN HEADER R/A 4POS 5.08MM | 1.8 | 1 | 1.8 | https://www.digikey.com/product-detail/en/te-connectivity-amp-connectors/641737-1/A25430-ND/289821
FANHDR: CONN HEADER VERT 4POS 2.54MM | 0.46 | 6 | 2.76 | https://www.digikey.com/products/en/connectors-interconnects/rectangular-connectors-headers-male-pins/314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
CAP ALUM 10UF 20% 50V THRU HOLE | 0.36 | 2 | 0.72 | https://www.digikey.com/product-detail/en/nichicon/ULD1H100MDD1TD/493-16250-1-ND/7365023
CAP CER 0.1UF 100V Z5U RADIAL | 0.31 | 3 | 0.93 | https://www.digikey.com/product-detail/en/kemet/C320C104M1U5TA7303/399-14023-1-ND/6562562
RES 10K OHM 1/4W 1% AXIAL | 0.1 | 5 | 0.5 | https://www.digikey.com/product-detail/en/stackpole-electronics-inc/RNF14FTD10K0/RNF14FTD10K0CT-ND/1975090
DIODE GEN PURP 100V 1A DO41 | 0.18 | 6 | 1.08 | https://www.digikey.com/product-detail/en/diodes-incorporated/1N4934-T/1N4934DICT-ND/190410
TEENSY 3.5 W/ HDRS K64 EVAL BRD | 31.25 | 1 | 31.25 | https://www.digikey.com/product-detail/en/sparkfun-electronics/DEV-14056/1568-1464-ND/6569368
CONN HDR 14POS 0.1 TIN PCB | 0.91 | 1 | 0.91 | https://www.digikey.com/product-detail/en/sullins-connector-solutions/PPTC141LFBN-RC/S7012-ND/810152
CONN HDR 15POS 0.1 TIN PCB | 0.98 | 1 | 0.98 | https://www.digikey.com/product-detail/en/sullins-connector-solutions/PPTC151LFBN-RC/S7013-ND/810153
CONN HDR 3POS 0.1 GOLD PCB | 0.37 | 1 | 0.37 | https://www.digikey.com/product-detail/en/sullins-connector-solutions/PPPC031LFBN-RC/S7036-ND/810175

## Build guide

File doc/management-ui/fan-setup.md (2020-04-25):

# Fan Setup

Fan speed configuration \(fe. control mode, temperature sensor source, etc.\).

Each available fan is individually configured:

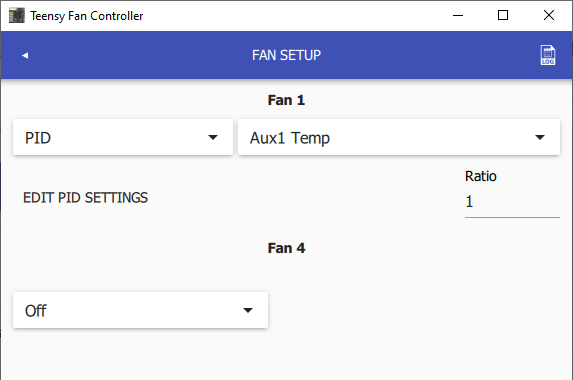
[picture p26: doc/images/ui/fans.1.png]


## Fan Operation

Fan operation / control mode (PID, Temp-% Table, Fixed, Off):

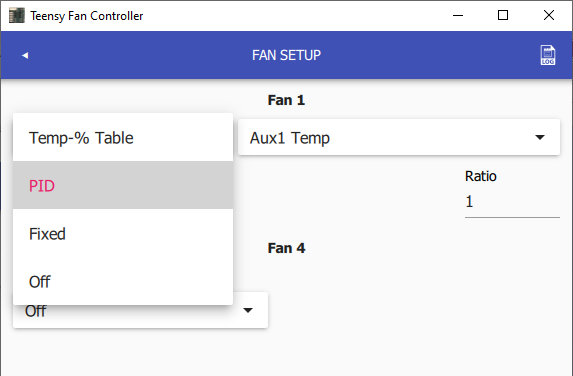
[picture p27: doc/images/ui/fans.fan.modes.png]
Fan Setup - Control modes


If a fan's control mode is set to **PID** or **Temp-% Table**, a sensor is configured:

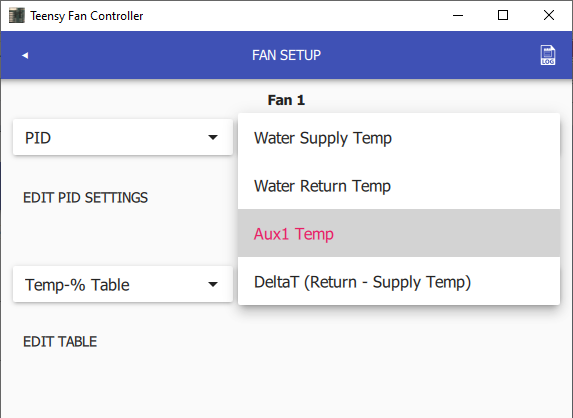
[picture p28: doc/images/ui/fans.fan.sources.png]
Fan Setup - Temperature sources


### Temp-% Table

TODO

If a fan's control mode is set to **Temp-% Table**, click **edit table** to configure the fan speed points:

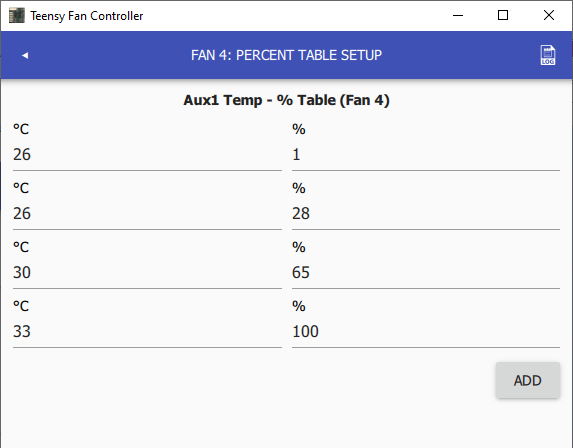
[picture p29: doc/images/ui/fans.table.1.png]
Fan Setup - Temp-% Table


### PID Setup

TODO

If a fan's control mode is set to **PID**, click **edit PID settings** to configure PID control:

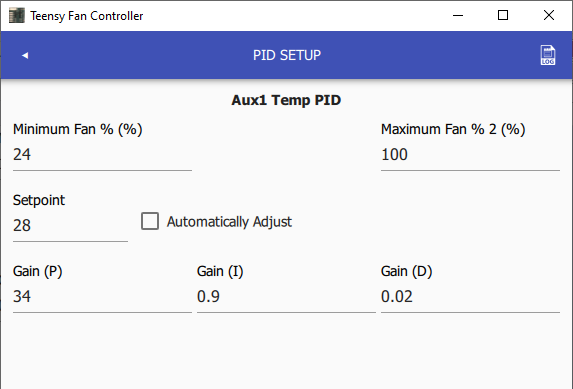
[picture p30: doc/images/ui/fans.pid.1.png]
Fan Setup - PID


Setpoint adjustment is enabled by checking **Automatically Adjust**:

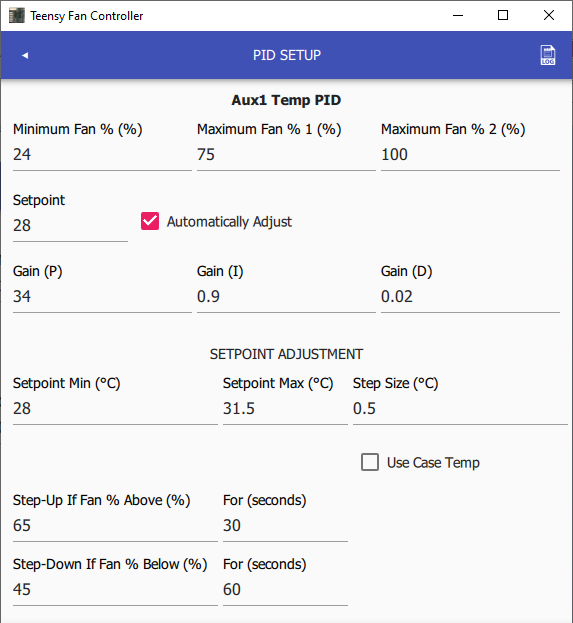
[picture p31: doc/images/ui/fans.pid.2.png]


Setpoint adjustment may be restricted by case temperature, by checking **Use Case Temp**:

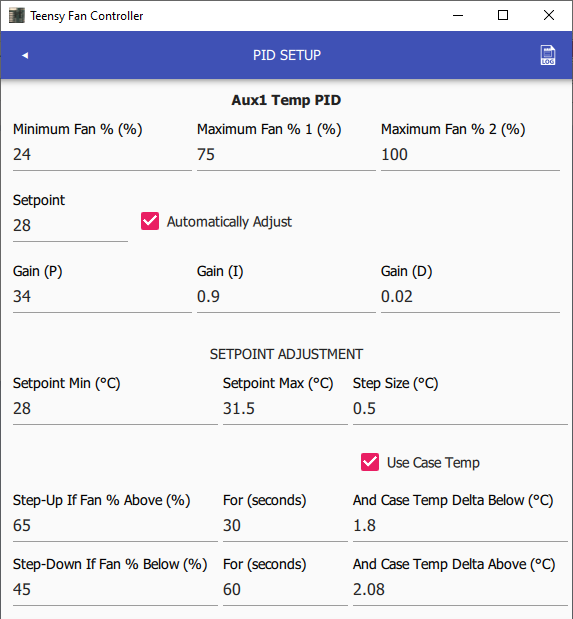
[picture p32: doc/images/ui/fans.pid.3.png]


## Saving Changes

Once configured, click **save** to upload the configuration onto the hardware:

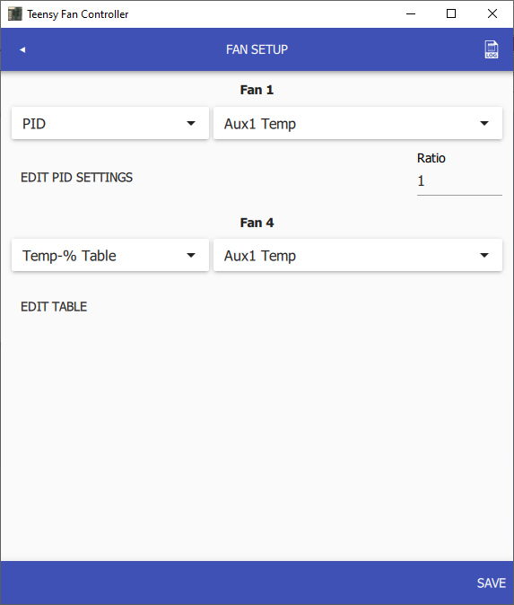
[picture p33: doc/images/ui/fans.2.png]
Fan Setup


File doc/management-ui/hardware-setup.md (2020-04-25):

# Hardware Setup

Hardware setup options for the Teensy Fan Controller \(fe. pin mapping, thermistor resistance, etc.\).

{% hint style="info" %}
Input fields on this screen are described when hovered with the mouse cursor.
{% endhint %}

## Temperature Sensors

Up to five \(5\) temperature sensors are supported, and labeled as supply water temp, return water temp, case temp, aux1 temp, and aux2 temp.

Hardware configuration options for each sensor:

| Field | Description |
| :--- | :--- |
| Pin | Teensy \(actual\) pin number \(must support Analog/ADC\). Set to **0 if not connected**, or to disable the sensor |
| Thermistor Beta Coefficient | Thermistor Beta coefficient, usually between 3000-4000 \(fe. 3950 NTC\) |
| Thermistor Nominal Resistance | Thermistor resistance, usually 10000 \(fe. 10k, 50k, etc.\) |
| Thermistor Series Resistance | Ohm value of series resistor used to pull-up thermistor, adjust this to calibrate reading \(use a 10k Ohm resistor for 10k thermistor\) |

### Sensor hardware setup

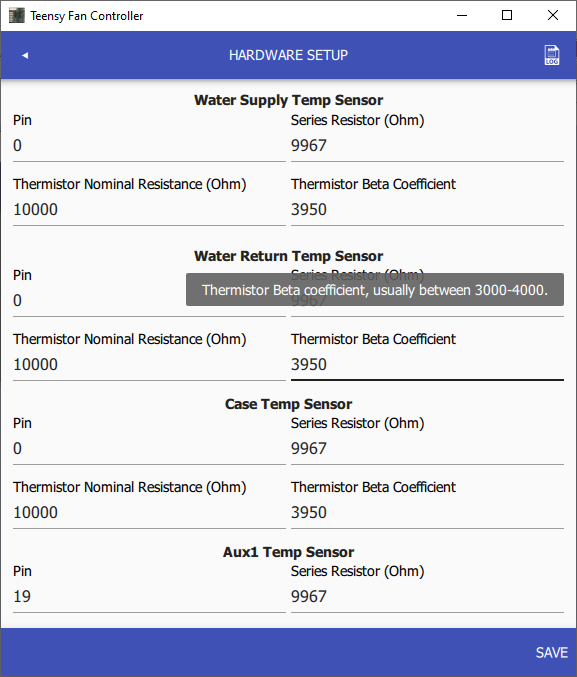
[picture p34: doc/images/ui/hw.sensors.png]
Hardware Setup - Sensors


## Fans

Up to six \(6\) fans are supported, and labeled by position \(fan 1 through fan 6\).

Hardware configuration options for each fan:

| Field | Description |
| :--- | :--- |
| PWM Pin | Teensy pin number \(must support PWM\). Set to **0 if not connected**, or to not control fan's PWM signal |
| RPM Pin | Teensy pin number \(must support interrupts\). Set to **0 if not connected**, or to not monitor fan's RPM |

### Fan hardware setup

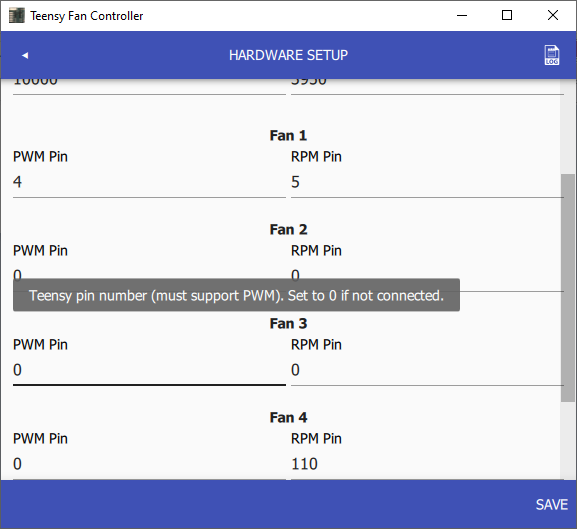
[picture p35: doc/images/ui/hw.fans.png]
Hardware Setup - Fans


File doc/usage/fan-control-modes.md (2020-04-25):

# Fan Control

Each fan individually configures a _control mode_.

The following _control modes_ are supported:

* PID
* Temperature-Percent Table \(%-table\)
* Fixed Percent
* Off

PID and %-table _control modes_ configure a _control source_, which represents what temperature sensor is used.

The following _control sources_ are supported:

* Water Supply Temperature
* Water Return Temperature
* Case Temperature
* Aux1 Temperature
* Aux2 Temperature

{% hint style="info" %}
By default, all fans operate in PID mode for supply water temperature control.
{% endhint %}

## Percent-Table Mode

Each fan may be individually configured to operate using its own _temperature to fan %-table_. This is like BIOS custom fan configurations.

Any one of the five temperature sensors, or DeltaT \(return temp - supply temp\), may be used as a temperature source.

## Fixed Mode

Each fan may be individually configured to operate using a fixed speed \(percent\).

## PID Control Mode

The PID controllers satisfy a temperature setpoint, by changing fan PWM duty cycle\(s\).

The fan controller may operate up to 4 PID controllers, one per the following temperature sensors: supply water temp, case temp, aux1 temp, and aux2 temp.

### _Setpoint Adjustment_ for Supply Water Temperature Control

Supply water temperature _setpoint adjustment_ is enabled by default, to handle room and/or case temperature changes. By default, the setpoint adjusts between 28°C and 31.5°C, at 0.25°C increments.

If a case temperature sensor is connected, _setpoint adjustment_ is limited by a difference between supply water and case temperature \(allowing fan spin-up when case temperature does not change\).

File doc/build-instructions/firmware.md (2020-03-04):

# Firmware \(Teensy\)

A Makefile and Arduino project for building the Teensy Fan Controller firmware. Sources are contained in the [teensy\_fan\_controller sub-folder](https://github.com/mstrthealias/TeensyFanController/tree/master/teensy_fan_controller).

{% hint style="info" %}
The Makefile and project structure is based on [Teensy 3.X Project Template](https://github.com/apmorton/teensy-template).
{% endhint %}

## Usage \(Makefile\)

1. Prepare the project \(once\), as described in [Project Setup](setup.md)
2. Enter the `teensy_fan_controller` directory:

   ```text
    cd teensy_fan_controller
   ```

3. Compile from source:

   ```text
    TEENSY=35 make
   ```

{% hint style="info" %}
Makefile generates a Teensy 3.2 build by default, you may use a different Teensy by setting the TEENSY variable \(either 30, 31, 32, 35, or 36\).
{% endhint %}

1. Upload to Teensy 3.x:

   ```text
     make upload
   ```

{% hint style="info" %}
Firmware Make targets:

* `make` alias for `make hex`
* `make build` compiles everything and produces a .elf
* `make hex` converts the elf to an intel hex file
* `make post_compile` opens the launcher with the correct file
* `make upload` uploads the hex file to a teensy board
* `make reboot` reboots the teensy
{% endhint %}

## Usage \(Arduino Studio\)

1. Prepare the project \(once\), as described in [Project Setup](setup.md)
2. Copy `teensy_fan_controller/libraries/nanopb` into your user's Arduino libraries folder \(fe. `~/Documents/Arduino/libraries/`\)
3. Copy `teensy_fan_controller/libraries/PID` into your user's Arduino libraries folder \(fe. `~/Documents/Arduino/libraries/`\)
4. Launch **Arduino Studio**, and open project **teensy\_fan\_controller/src/src.ino**
5. Set **Tools &gt; Board** to your Teensy board using the top menu
6. Set **Tools &gt; USB Type** to **Raw HID** using the top menu
7. Build and upload firmware using **Sketch &gt; Upload**, or by clicking the **Upload** button in the toolbar

### Folder Structure

After the project is prepared, the `teensy_fan_controller/` folder has the following structure:

* `teensy3` sub-folder is taken from [The Teensy 3 Cores](https://github.com/PaulStoffregen/cores/tree/master/teensy3)
* `tools` sub-folder is taken from [Teensyduino](http://www.pjrc.com/teensy/td_download.html)
* `src/src.ino` contains the `loop()` and `setup()` functions, called by `teensy3/main.cpp`
* `src/*.{ino,c,h,cpp}` Teensy Fan Controller sources
* `Makefile` file, copied and modified from `teensy3/Makefile`
* `49-teensy.rules` file is taken from [PJRC's udev rules](http://www.pjrc.com/teensy/49-teensy.rules)

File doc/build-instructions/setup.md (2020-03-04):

# Project Setup

## Software Requirements

The following software is required to build the project:

### Windows

* [Arduino](https://www.arduino.cc/en/Main/Software) installation with [Teensyduino](https://www.pjrc.com/teensy/teensyduino.html) add-on
* Git for Windows \(Bash\)
* MinGW \(make\)
* Visual Studio 2017 \(for Management UI builds\)
* Qt 5 \(for Management UI builds\)

{% hint style="info" %}
This project uses Makefile, however build tools and board files are copied from an [Arduino](https://www.arduino.cc/en/Main/Software)/[Teensyduino](https://www.pjrc.com/teensy/teensyduino.html) installation.
{% endhint %}

{% hint style="warning" %}
If needed, copy `MinGW/bin/mingw32-make.exe` to `MinGW/bin/make.exe`, as this documentation refers to the command as `make`.
{% endhint %}

Requirements to regenerate protobuf \([nanopb](https://github.com/nanopb/nanopb)\) sources:

1. Download protoc binaries, fe.: [https://github.com/protocolbuffers/protobuf/releases/download/v3.11.4/protoc-3.11.4-win64.zip](https://github.com/protocolbuffers/protobuf/releases/download/v3.11.4/protoc-3.11.4-win64.zip)
2. Extract zip, fe. c:\share\protoc-3.11.4
3. Add protoc \(fe., c:\share\protoc-3.11.4\bin\) to PATH

### Ubuntu 18.04

* [Arduino](https://www.arduino.cc/en/Main/Software) installation with [Teensyduino](https://www.pjrc.com/teensy/teensyduino.html) add-on
* `apt install build-essential`
* Qt 5 \(for Management UI builds\)

{% hint style="info" %}
This project uses Makefile, however build tools and board files are copied from an [Arduino](https://www.arduino.cc/en/Main/Software)/[Teensyduino](https://www.pjrc.com/teensy/teensyduino.html) installation.
{% endhint %}

Requirements to regenerate protobuf \([nanopb](https://github.com/nanopb/nanopb)\) sources:

* `apt install protobuf libprotobuf-dev python-protobuf`

{% hint style="info" %}
To communicate with the Teensy hardware as a **non-root user**, install the [Teensy udev rule](https://www.pjrc.com/teensy/49-teensy.rules):

```text
sudo cp teensy_fan_controller/tools/49-teensy.rules /etc/udev/rules.d/
```
{% endhint %}

## Fetching sources

Use `git` to clone the root project \([TeensyFanController](https://github.com/mstrthealias/TeensyFanController)\).

You must initialize and pull the git sub-modules/sub-repositories:

```text
git clone https://github.com/mstrthealias/TeensyFanController.git
git submodule init
git submodule update
```

{% hint style="info" %}
Use the `ui_qt5` sub-directory underneath the root project directory for Management UI builds.
{% endhint %}

## Setup project build environment

Change directory to the project root, and use Makefile:

```text
cd TeensyFanController
ARDUINO_DIR=/opt/Arduino make
```

{% hint style="info" %}
Root Make targets:

* `make` alias for `make setup`
* `make setup` alias for `make clean setup-toolchain setup-libs setup-nanopb protos`
* `make setup-toolchain` copy toolchain and Teensy3 cores from [Teensyduino](https://www.pjrc.com/teensy/teensyduino.html) into project
* `make setup-libs` copy [Teensyduino](https://www.pjrc.com/teensy/teensyduino.html) libraries into project
* `make setup-nanopb` copy [nanopb](https://github.com/nanopb/nanopb) into project libraries
* `make protos` alias for `make runtime_config_v1.pb.c`
* `make runtime_config_v1.pb.c` generate RuntimeConfigV1 protobuf sources
* `make clean` alias for `make clean-build clean-setup`
* `make clean-build` delete builds produced by `teensy_fan_controller/Makefile`
* `make clean-setup` delete files produced by this Makefile
{% endhint %}

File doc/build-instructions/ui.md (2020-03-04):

# Management UI

{% hint style="warning" %}
You should have cloned the [root project](https://github.com/mstrthealias/TeensyFanController) and it's sub-modules \(which includes this project directory\).

That-way the **parent directory** contains the **HIDAPI** and **teensy\_fan\_controller** projects.
{% endhint %}

## Windows

Prerequisites:

1. Qt Installer
2. MSVC 2017 64-bit
3. Recent Qt release \(Qt 5.13.2 at time of writing\) for MSVC 2017 64-bit
4. Qt Charts component

{% hint style="warning" %}
The application is NOT compatible with MinGW builds due to the use of [hidapi](https://github.com/libusb/hidapi). HIDAPI will compile with mingw32 \(NOT mingw64-32bit\), however Qt must be built from source to use this stack.
{% endhint %}

Note:

First, build the static [HIDAPI](https://github.com/mstrthealias/HIDAPI-Qt5) library:

1. Launch **x64 Native Tools Command Prompt for VS 2017**
2. Add Qt5 to PATH, fe.:

   ```text
    SET PATH=%PATH%;c:\share\Qt\5.13.2\msvc2017_64\bin
   ```

3. Change directory to HIDAPI
4. Run qmake:

   ```text
    qmake
   ```

5. Run nmake:

   ```text
    nmake
   ```

6. Verify HIDAPI.lib was created:

   ```text
        dir windows\HIDAPI.lib

        ...
        12/30/2019  11:03 AM            27,960 HIDAPI.lib
   ```

Building the Fan Controller UI:

{% hint style="warning" %}
Until the Fan Controller UI's installer is published, it is easiest to run the application using Qt Creator.

You may build using the CLI with qmake and nmake, but will have to copy all Qt runtime dependencies \(qml, plugins, dlls\) into the release directory to start the application.
{% endhint %}

## Linux \(Ubuntu 18.04\)

Prerequisites:

1. Qt Installer
2. Recent Qt release \(Qt 5.13.2 at time of writing\) for GCC 64-bit
3. Qt Charts component
4. `apt install build-essential libxkbcommon-x11-0 libhidapi-dev libhidapi-hidraw0 libgl1 libgl1-mesa-dev libx11-xcb1`

{% hint style="info" %}
I experienced issues launching the application using X11 forwarding and ended up installing and launching xfce \(`apt install xfce4`\).
{% endhint %}

First, build the static [HIDAPI](https://github.com/mstrthealias/HIDAPI-Qt5) library:

1. In non-root Shell, add Qt5 to PATH, fe.:

   ```text
    PATH=$PATH:~/Qt/5.13.2/gcc_64/bin
    QT_QPA_PLATFORM_PLUGIN_PATH=~/Qt/5.13.2/gcc_64/plugins
   ```

2. Change directory to HIDAPI, fe.:

   ```text
    cd ~/TeensyFanController/HIDAPI
   ```

3. Run qmake:

   ```text
    qmake
   ```

4. Run make:

   ```text
    make
   ```

5. Verify libHIDAPI.a was created:

   ```text
    ls linux/libHIDAPI.a
   ```

Build the Fan Controller UI:

1. Change directory to HIDAPI, fe.:

   ```text
    cd ~/TeensyFanController/teensy_fan_controller
   ```

2. Run qmake:

   ```text
    qmake
   ```

3. Run make:

   ```text
    make
   ```

4. Launch using `sudo` \(note: replace /home/username/Qt/5.13.2 with path to Qt release\):

   ```text
    sudo bash -c 'QT_BASE=/home/username/Qt/5.13.2 QML2_IMPORT_PATH="$QT_BASE/gcc_64/qml" QML_IMPORT_PATH="$QT_BASE/gcc_64/qml" QT_QPA_PLATFORM_PLUGIN_PATH="$QT_BASE/gcc_64/plugins"  ./tfctrl'
   ```

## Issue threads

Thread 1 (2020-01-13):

Advanced configuration

mstrthealias, 2020-01-13:
Support advanced fan configuration(s), to provide a complete fan controller, with an ABI more similar to those controlled by liquidctl:

- Multiple PID support (1 PID per temperature sensor)
- Multiple temperature-fan % table support (table per fan/not-profile based)
- Fixed speed support

Technical details (in collaboration with Jonas @ liquidctl):

Notes:
- %-table is saved in each fan config
- PID config is saved in each sensor config

FanConfig->source (CONTROL_SOURCE):
- WATER_SUPPLY_TEMP
- WATER_RETURN_TEMP
- CASE_TEMP
- AUX1_TEMP
- AUX2_TEMP
- VIRTUAL_DELTA_TEMP

FanConfig->mode (CONTROL_MODE):
- TBL
- PID
- FULL

Closed 2020-03-08.

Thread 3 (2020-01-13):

Documentation

mstrthealias, 2020-01-13:
Complete an initial version of documentation:

- Usage/Getting Started
- Example data
- Detailed configuration
- PID tuning
- Hardware constraints (fe. no-save on Teensy LC, pin setup, etc.)

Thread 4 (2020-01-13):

First release

mstrthealias, 2020-01-13:
- Firmware (pre-built) for Teensy LC/3.5/3.6/3.2
- Flash instructions
- UI/Qt application release (pre-built, signed?)

Related requirements:

- #1 (Advanced configuration)
- #3 (Documentation)
- #5 Circuit schematic (or wiring diagram)
- #5 PCB layout?

Closed 2020-04-25.

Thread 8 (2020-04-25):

Schematic and PCB (Simple002)

mstrthealias, 2020-04-25:
Improve Simple001:

- Correct board mount hole locations
- Add jumpers or solder bridges to support 6th fan PWM on Teensy LC, 3.2, 3.5, 3.6, and 4.0
- Remove AREF<>VCC jumper
- Remove AGND<>GND solder bridge?

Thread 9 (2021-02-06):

Working with Arch.....Teensy 4.0?

blazini36, 2021-02-06:
Not sure if these are distro issues, or just issues in general. Trying to follow the istructions @ [https://mstrthealias.gitbook.io/teensy-fan-controller/build-instructions/setup](url), can't really get anywhere.
```
git clone https://github.com/mstrthealias/TeensyFanController.git
git submodule init
git submodule update
```
looks like it needs to be
```
git clone https://github.com/mstrthealias/TeensyFanController.git
cd TeensyFanController
git submodule init
git submodule update
```
However, $ git submodule update throws all sorts of publickey errors. Assuming that command wasn't 100% necessary:
```
~$ cd TeensyFanController/
TeensyFanController$ ARDUINO_DIR=/opt/Arduino make
Makefile:12: *** Invalid ARDUINO_DIR.  Stop.
```
Thats as far as I got with that. Trying to build the compile the Arduino project right in Arduino IDE didn't work either. (Using "Teensyduino"). Here I tried it with a board setup for Teensy 4.0 which I would hope to be able to use, but it failed for 3.x as well.

Arduino: 1.8.13 (Linux), TD: 1.53, Board: "Teensy 4.0, Serial, 600 MHz, Faster, US English"

In file included from /tmp/arduino_build_491770/sketch/runtime_config.h:20:0,
                 from /home/justin/TeensyFanController/teensy_fan_controller/src/src.ino:3:
/tmp/arduino_build_491770/sketch/runtime_config_v1.pb.h:6:16: fatal error: pb.h: No such file or directory
compilation terminated.
Error compiling for board Teensy 4.0.

blazini36, 2021-02-06:
Actually I got a bit further once I somewhat figured out what I was doing. Have to run "git init" here

```
git clone https://github.com/mstrthealias/TeensyFanController.git
git init
git submodule init
git submodule update
```
Also had to change the makefile targets a bit and provide the nanopb source, and manually create the working directories for whatever reason. I getting stuck on line 87 yet, not sure what to do here.

```
$ make                                                                                                                                                      1 ✘

Cleaning build...
rm -rf /home/justin/git/TeensyFanController/teensy_fan_controller/build/*
rm -f /home/justin/git/TeensyFanController/teensy_fan_controller/src/nanopb.proto
rm -f /home/justin/git/TeensyFanController/teensy_fan_controller/src/runtime_config_v1.pb.c
rm -f /home/justin/git/TeensyFanController/teensy_fan_controller/src/runtime_config_v1.pb.h

Cleaning project...
rm -rf /home/justin/git/TeensyFanController/teensy_fan_controller/libraries/nanopb
rm -rf /home/justin/git/TeensyFanController/teensy_fan_controller/libraries/EEPROM
rm -rf /home/justin/git/TeensyFanController/teensy_fan_controller/tools/*
rm -rf /home/justin/git/TeensyFanController/teensy_fan_controller/teensy3/*

Copy Teensy tools into project...
cp /usr/share/arduino/hardware/tools/teensy* /home/justin/git/TeensyFanController/teensy_fan_controller/tools/
cp /usr/share/arduino/hardware/tools/precompile_helper* /home/justin/git/TeensyFanController/teensy_fan_controller/tools/
cp /usr/share/arduino/hardware/tools/stdout_redirect* /home/justin/git/TeensyFanController/teensy_fan_controller/tools/
cp /usr/share/arduino/hardware/tools/mktinyfat* /home/justin/git/TeensyFanController/teensy_fan_controller/tools/
cp -a /usr/share/arduino/hardware/tools/arm /home/justin/git/TeensyFanController/teensy_fan_controller/tools/
touch /home/justin/git/TeensyFanController/teensy_fan_controller/tools/.gitkeep

Copy Teensy 3.x cores into project...
cp -a /usr/share/arduino/hardware/teensy/avr/cores/teensy3/* /home/justin/git/TeensyFanController/teensy_fan_controller/teensy3/
touch /home/justin/git/TeensyFanController/teensy_fan_controller/teensy3/.gitkeep

Copy libraries into project...
cp -a /usr/share/arduino/hardware/teensy/avr/libraries/EEPROM /home/justin/git/TeensyFanController/teensy_fan_controller/libraries/
touch /home/justin/git/TeensyFanController/teensy_fan_controller/libraries/EEPROM/.gitkeep
mkdir /home/justin/git/TeensyFanController/teensy_fan_controller/libraries/nanopb
cp /home/justin/git/TeensyFanController/nanopb/*.{h,c} /home/justin/git/TeensyFanController/teensy_fan_controller/libraries/nanopb/
touch /home/justin/git/TeensyFanController/teensy_fan_controller/libraries/nanopb/.gitkeep

Building protobufs
cp /home/justin/git/TeensyFanController/nanopb/generator/proto/nanopb.proto /home/justin/git/TeensyFanController/teensy_fan_controller/src/
proto_path=/home/justin/git/TeensyFanController/teensy_fan_controller/src/ --nanopb_out=/home/justin/git/TeensyFanController/teensy_fan_controller/src/ /home/justin/git/TeensyFanController/teensy_fan_controller/src/runtime_config_v1.proto
/bin/sh: line 1: --nanopb_out=/home/justin/git/TeensyFanController/teensy_fan_controller/src/: No such file or directory
make: [Makefile:87: runtime_config_v1.pb.c] Error 127 (ignored)
```
I realize that the makefile at least isn't configured for teensy4.x. I'd pick up a 3.x for now if I could at least get it built.

mstrthealias, 2024-04-24:
Just came across your post today.  What distro were you using, that-way I can diagnose the problem?

It looks like you may have just needed to `mkdir teensy_fan_controller/src` to avoid that error.

I did try the project on a Teensy 4 but had some issues with the RPMs being reported as twice the expected value; I suspect this issue is fixed in the Teensy libraries today.  In order to support Teensy 4.1, you'd have to modify `teensy_fan_controller/Makefile`, set `TEENSY=41`, and add a block to the if statements to correct `CPPFLAGS`, `LDSCRIPT`, and `LDFLAGS` for the Teensy 4.1.

Thanks for trying the project, and sorry for the late response...

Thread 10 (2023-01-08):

Schematic: fan pin assignments

msladen, 2023-01-08:
Hi Jack,
I have a project that I set aside, and am just getting back to.  Amplifier controller, but it incorporates a fan control, and I was looking at your project for reference.  I saw that on your schematic you show power and ground going into the fan through pins 3 and 4 respectively.  Other documentation shows pins 2 and 1 for 12v and ground, including the original Intel pwm document,  Since these are often implemented in headers that can be plugged in either way, it may not matter, but plugging the connector in the wrong way will probably fry it.  Suggest you change the pin designations on your schematic.

mstrthealias, 2024-04-24:
I suspect that I incorrectly named/ordered the pins as 4 through 1 instead of 1 through 4.  The actual hardware should be correct (has worked for me for years), and I can correct this in the schematic for the Simple 003 schematics.

Thanks for reviewing the project.

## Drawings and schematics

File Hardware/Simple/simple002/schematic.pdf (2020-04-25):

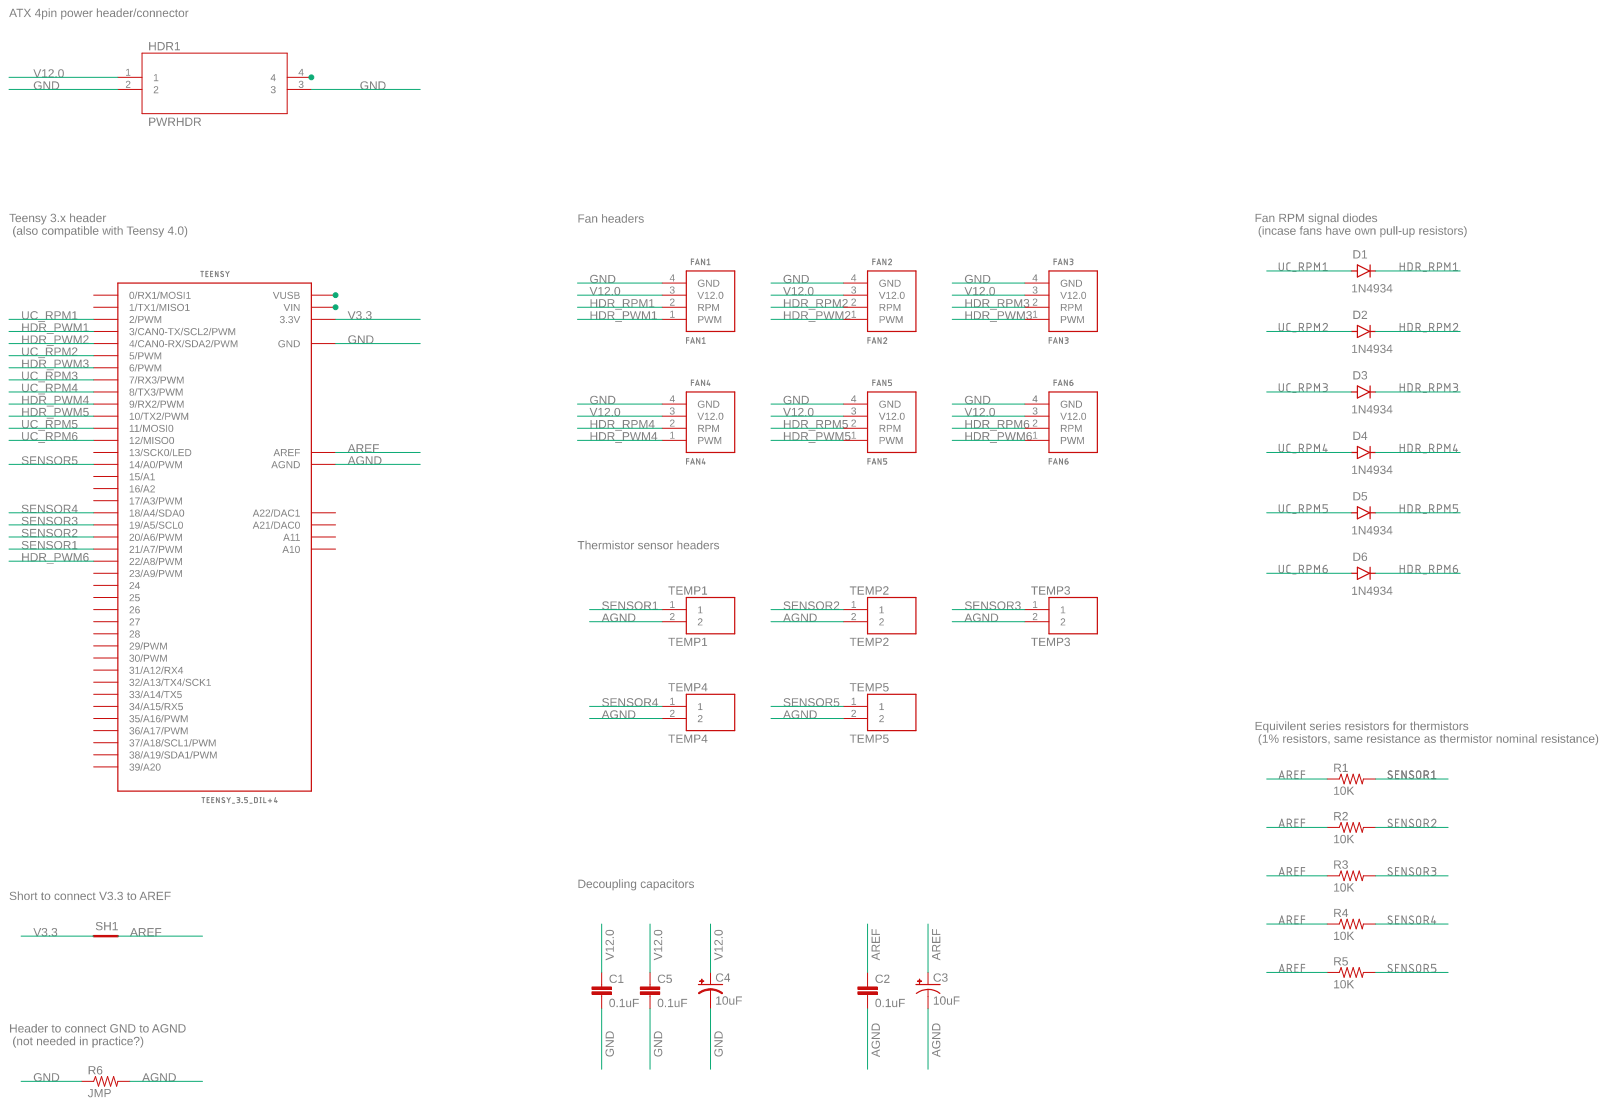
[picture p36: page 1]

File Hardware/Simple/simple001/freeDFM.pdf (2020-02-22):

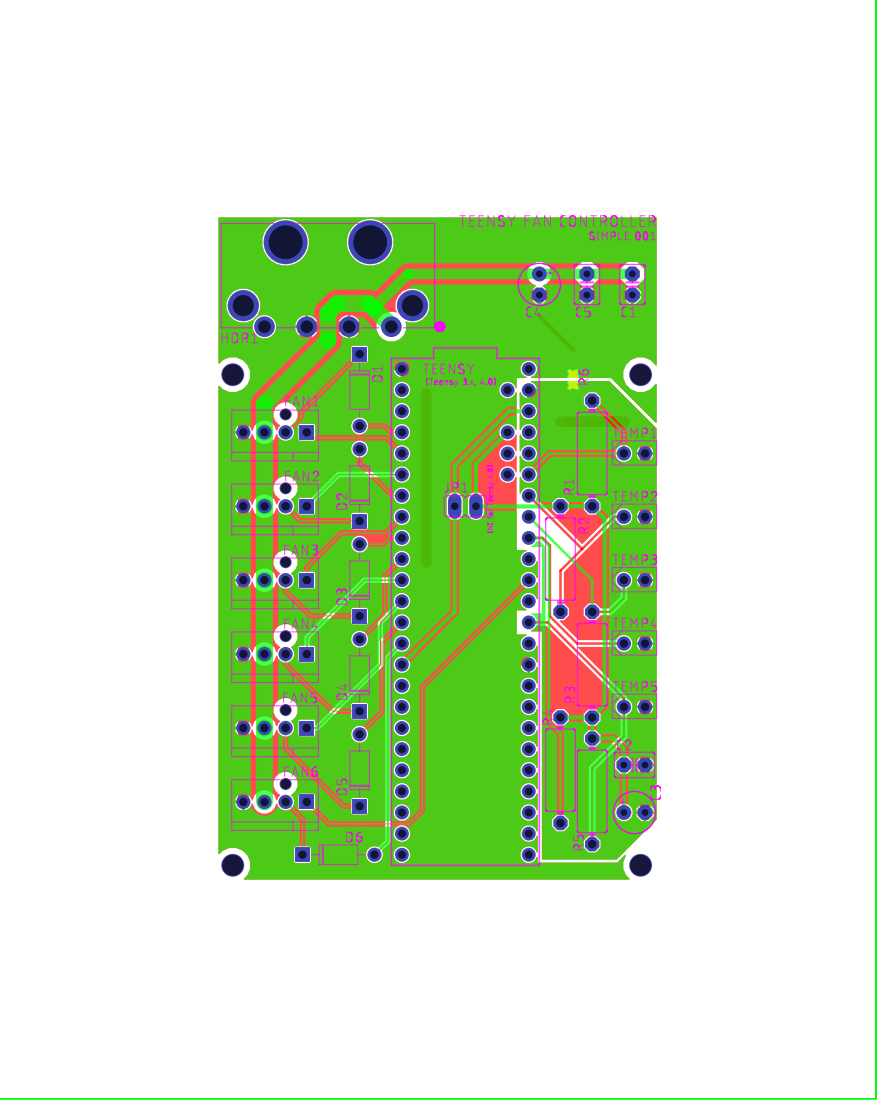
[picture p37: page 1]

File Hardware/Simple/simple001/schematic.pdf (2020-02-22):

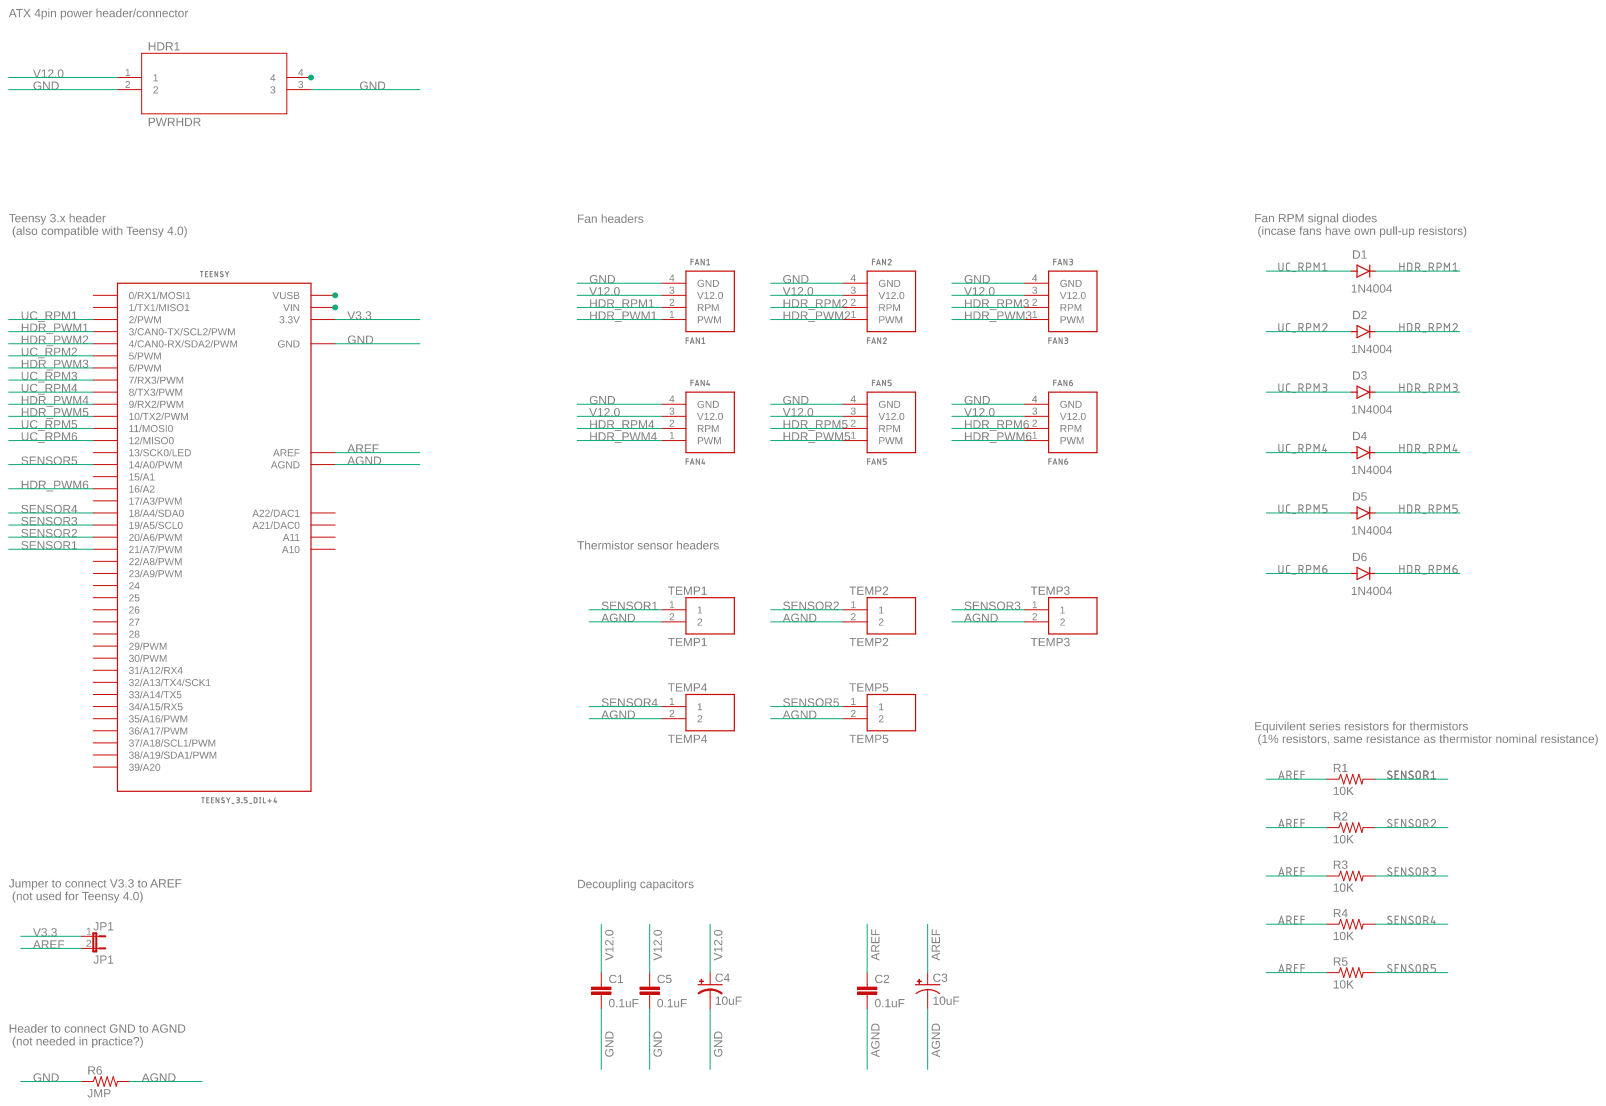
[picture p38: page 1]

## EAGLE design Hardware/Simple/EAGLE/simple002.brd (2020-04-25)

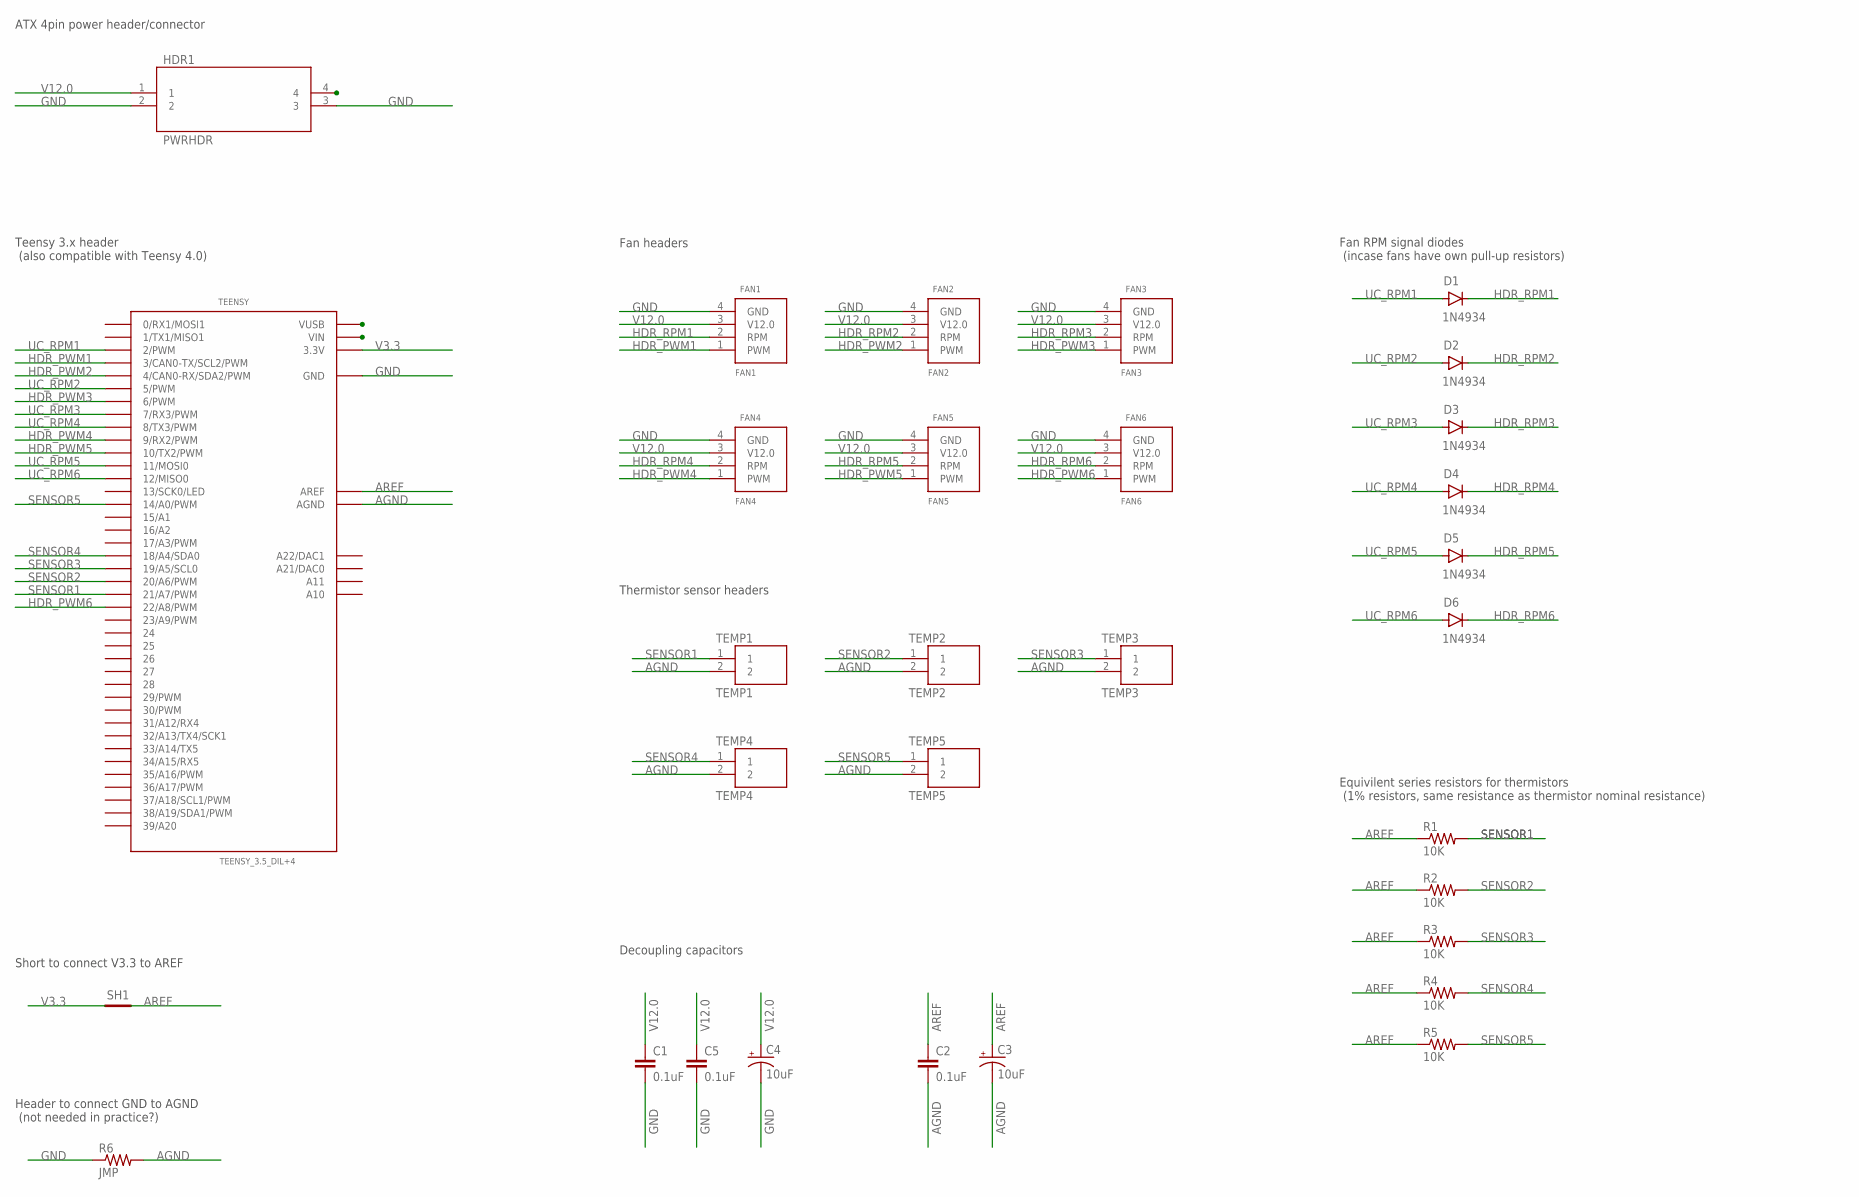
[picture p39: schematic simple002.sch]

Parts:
C1, C2, C5: 0.1uF; C2.5-3; MANUFACTURER_PART_NUMBER C320C104M1U5TA7303; DIGIKEY_PART_NUMBER 399-14023-1-ND
C3, C4: 10uF; E2,5-5; MANUFACTURER_PART_NUMBER ULD1H100MDD1TD; DIGIKEY_PART_NUMBER 493-16250-1-ND
D1, D2, D3, D4, D5, D6: 1N4934; DO-41
FAN1: FAN1; FAN4
FAN2: FAN2; FAN4
FAN3: FAN3; FAN4
FAN4: FAN4
FAN5: FAN5; FAN4
FAN6: FAN6; FAN4
HDR1: PWRHDR; 641737-1
R1, R2, R3, R4, R5: 10K; V234/12; MANUFACTURER_PART_NUMBER RNF14FTD10K0; DIGIKEY_PART_NUMBER RNF14FTD10K0CT-ND
R6: JMP; R0402
SH1: SHORTT5; SHORT_TOP-50
TEENSY: TEENSY_3.5_DIL+4; MANUFACTURER_PART_NUMBER DEV-14056; DIGIKEY_PART_NUMBER 1568-1464-ND
TEMP1: TEMP1; SENSOR2
TEMP2: TEMP2; SENSOR2
TEMP3: TEMP3; SENSOR2
TEMP4: TEMP4; SENSOR2
TEMP5: TEMP5; SENSOR2

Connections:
AGND: C2.2, C3.-, R6.2, TEENSY.AGND, TEMP1.2, TEMP2.2, TEMP3.2, TEMP4.2, TEMP5.2
AREF: C2.1, C3.+, R1.1, R2.1, R3.1, R4.1, R5.1, SH1.2, TEENSY.AREF
GND: C1.2, C4.-, C5.2, FAN1.4 (GND), FAN2.4 (GND), FAN3.4 (GND), FAN4.4 (GND), FAN5.4 (GND), FAN6.4 (GND), HDR1.2, HDR1.3, R6.1, TEENSY.GND, TEENSY.GND1 (GND)
HDR_PWM1: FAN1.1 (PWM), TEENSY.3 (3/CAN0-TX/SCL2/PWM)
HDR_PWM2: FAN2.1 (PWM), TEENSY.4 (4/CAN0-RX/SDA2/PWM)
HDR_PWM3: FAN3.1 (PWM), TEENSY.6 (6/PWM)
HDR_PWM4: FAN4.1 (PWM), TEENSY.9 (9/RX2/PWM)
HDR_PWM5: FAN5.1 (PWM), TEENSY.10 (10/TX2/PWM)
HDR_PWM6: FAN6.1 (PWM), TEENSY.22/A8 (22/A8/PWM)
HDR_RPM1: D1.C, FAN1.2 (RPM)
HDR_RPM2: D2.C, FAN2.2 (RPM)
HDR_RPM3: D3.C, FAN3.2 (RPM)
HDR_RPM4: D4.C, FAN4.2 (RPM)
HDR_RPM5: D5.C, FAN5.2 (RPM)
HDR_RPM6: D6.C, FAN6.2 (RPM)
NC_VIN: TEENSY.VIN
NC_VUSB: TEENSY.VUSB
SENSOR1: R1.2, TEENSY.21/A7 (21/A7/PWM), TEMP1.1
SENSOR2: R2.2, TEENSY.20/A6 (20/A6/PWM), TEMP2.1
SENSOR3: R3.2, TEENSY.19/A5 (19/A5/SCL0), TEMP3.1
SENSOR4: R4.2, TEENSY.18/A4 (18/A4/SDA0), TEMP4.1
SENSOR5: R5.2, TEENSY.14/A0 (14/A0/PWM), TEMP5.1
UC_RPM1: D1.A, TEENSY.2 (2/PWM)
UC_RPM2: D2.A, TEENSY.5 (5/PWM)
UC_RPM3: D3.A, TEENSY.7 (7/RX3/PWM)
UC_RPM4: D4.A, TEENSY.8 (8/TX3/PWM)
UC_RPM5: D5.A, TEENSY.11 (11/MOSI0)
UC_RPM6: D6.A, TEENSY.12 (12/MISO0)
V3.3: SH1.1, TEENSY.3.3V, TEENSY.3.3V3 (3.3V)
V12.0: C1.1, C4.+, C5.1, FAN1.3 (V12.0), FAN2.3 (V12.0), FAN3.3 (V12.0), FAN4.3 (V12.0), FAN5.3 (V12.0), FAN6.3 (V12.0), HDR1.1

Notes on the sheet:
Header to connect GND to AGND (not needed in practice?)
Short to connect V3.3 to AREF
Equivilent series resistors for thermistors (1% resistors, same resistance as thermistor nominal resistance)
Fan headers
Thermistor sensor headers
ATX 4pin power header/connector
Teensy 3.x header (also compatible with Teensy 4.0)
Fan RPM signal diodes (incase fans have own pull-up resistors)
Decoupling capacitors

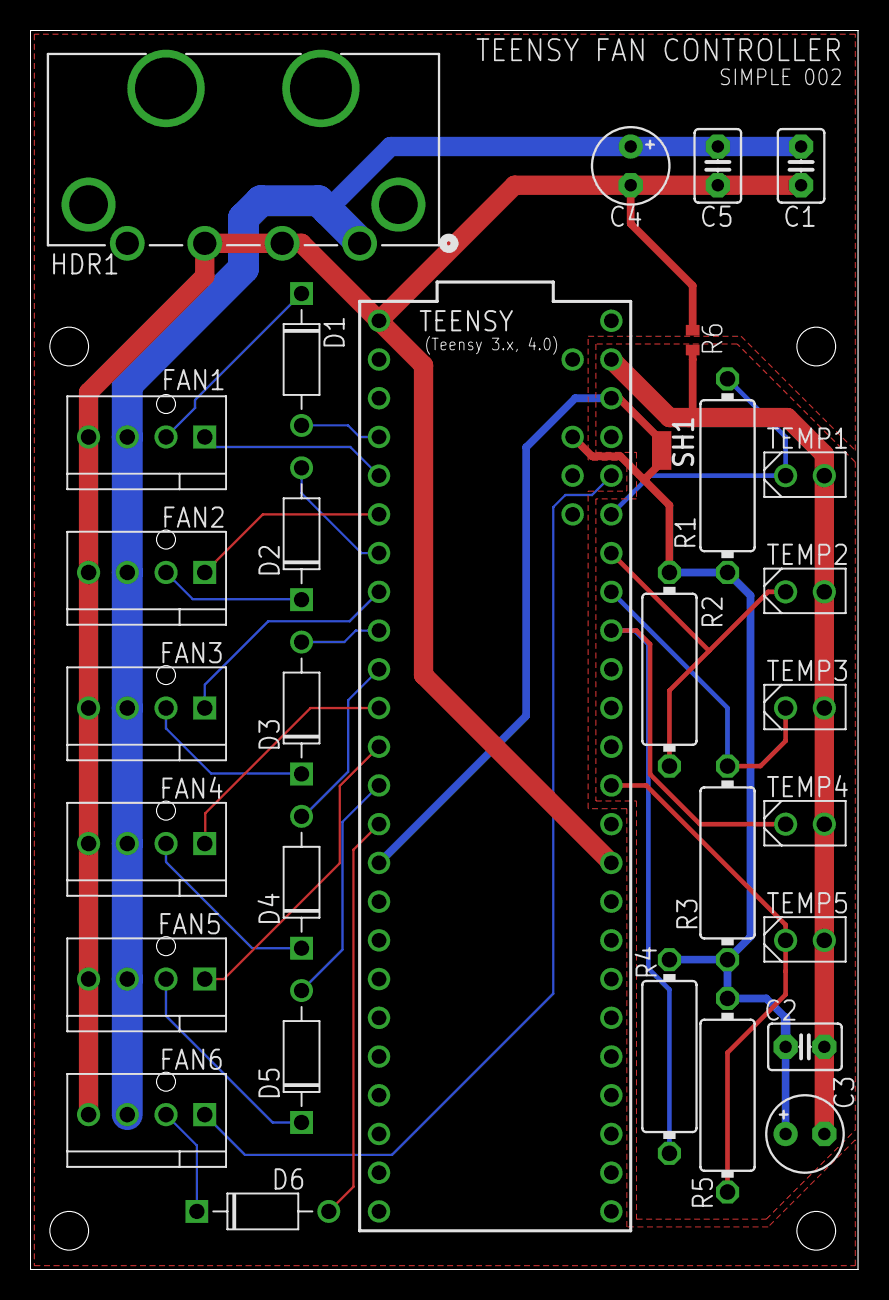
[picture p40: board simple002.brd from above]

Board: 2 copper layers, 54.3 x 81.3 mm, 31 parts (0 on the bottom side), 28 nets.

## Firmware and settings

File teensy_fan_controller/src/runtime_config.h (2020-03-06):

//
// Created by jd on 11/26/2019.
//

#ifndef TFC_RUNTIMECONFIG_H
#define TFC_RUNTIMECONFIG_H

#ifdef ARDUINO
#include <Arduino.h>
#else
#include <cstdint>
#include <cstddef>
typedef unsigned char byte;
#define A3 0
#define A4 0
#define A6 0
#define A7 0
#endif

#include "runtime_config_v1.pb.h"


// thermistor coefficients/defaults
#define TEMPERATURENOMINAL 25  // temp. for thermistor nominal resistance
#define DEFAULT_BCOEFFICIENT 3950  // Default beta coefficient of the thermistor (usually 3000-4000)
#define DEFAULT_SERIESRESISTOR 9377  // Default value of the 'other' resistor
#define DEFAULT_THERMISTORNOMINAL 10000  // Default thermistor nominal resistence (at nominal temp)

// core related constants
#define FAN_TBL_SIZE 10
#define FAN_CNT 6

// config related constants
#define CONTROLLER_VERSION 1  // use to flag the version of configuration saved
#define CONFIG_KEY1 0x2C  // use to flag a valid config
#define CONFIG_KEY2 0x30  // use to flag a valid config

#define CONFIG_POS_VERSION              0
#define CONFIG_POS_KEY1                 1
#define CONFIG_POS_KEY2                 2
#define CONFIG_POS_CONFIG_LENGTH        4  // spans 2 bytes
#define CONFIG_POS_CONFIG               6

#define CONFIG_BYTES 1008
#define CHUNK_SIZE 56
#define CHUNK_CNT 18


enum class CONTROL_MODE : uint8_t {
  MODE_TBL,
  MODE_PID,
  MODE_FIXED,
  MODE_OFF
};

tfcproto_ControlMode CONTROL_MODE_to_proto(CONTROL_MODE in);

CONTROL_MODE CONTROL_MODE_from_proto(const tfcproto_ControlMode &in);


enum class CONTROL_SOURCE : uint8_t {
  SENSOR_WATER_SUPPLY_TEMP,
  SENSOR_WATER_RETURN_TEMP,
  SENSOR_CASE_TEMP,
  SENSOR_AUX1_TEMP,
  SENSOR_AUX2_TEMP,
  VIRTUAL_DELTA_TEMP,
};

tfcproto_ControlSource CONTROL_SOURCE_to_proto(CONTROL_SOURCE in);

CONTROL_SOURCE CONTROL_SOURCE_from_proto(const tfcproto_ControlSource &in);


/**
   Fan controller's runtime configuration struct.
*/
struct RuntimeConfig {
  struct TableConfig {
    float temp_pct_table[FAN_TBL_SIZE][2];

    tfcproto_TableConfigV1 toProto() const;

    static TableConfig from_proto(tfcproto_TableConfigV1 &in);
  };
  struct FanConfig {
    uint8_t pinPWM;
    uint8_t pinRPM;
    CONTROL_MODE mode;
    CONTROL_SOURCE source;
    float ratio;
    TableConfig tbl;

    tfcproto_FanConfigV1 toProto() const;

    static FanConfig from_proto(tfcproto_FanConfigV1 &in);
  };
  struct PIDConfig {
    struct PIDStep {
      uint8_t pct;
      uint16_t delay;  // # of seconds fan % must be below step_down_pct to step setpoint down 0.5C
      float case_temp_delta;  // require (case_temp <= setpoint - <delta>) to step down setpoint

      tfcproto_PIDStepV1 toProto() const;

      static PIDStep from_proto(tfcproto_PIDStepV1 &in);
    };

    uint8_t pwm_percent_min;
    uint8_t pwm_percent_max1;
    uint8_t pwm_percent_max2;

    float setpoint;  // Default Setpoint
    float setpoint_min;
    float setpoint_max;

    // PID Tunings
    //double Kp=39, Ki=1.61, Kd=0.05;  // sheet5  // 100ms, ideal for router cooling experiment
    //double Kp = 39, Ki = 1.03, Kd = 0.03; // sufficient for 360+120 radiators aggresive tunings
    uint8_t gain_p;  //39
    float gain_i;  //1.03f
    float gain_d;  //0.03f

    bool adaptive_sp;  // adapt setpoint by 0.5C within setpoint_min >= setpoint >= setpoint_max
    bool adaptive_sp_check_case_temp;
    float adaptive_sp_step_size;
    PIDStep adaptive_sp_step_down;
    PIDStep adaptive_sp_step_up;

    tfcproto_PIDConfigV1 toProto() const;

    static PIDConfig from_proto(tfcproto_PIDConfigV1 &in);
  };
  struct SensorConfig {
    uint8_t pin;
    uint16_t beta;
    uint16_t seriesR;
    uint16_t nominalR;
    PIDConfig pid;

    tfcproto_SensorConfigV1 toProto() const;

    static SensorConfig from_proto(tfcproto_SensorConfigV1 &in);
  };

  uint8_t config_version;

  FanConfig fan1;
  FanConfig fan2;
  FanConfig fan3;
  FanConfig fan4;
  FanConfig fan5;
  FanConfig fan6;

  SensorConfig tempSupply;
  SensorConfig tempReturn;
  SensorConfig tempCase;
  SensorConfig tempAux1;
  SensorConfig tempAux2;

  RuntimeConfig();
  RuntimeConfig(uint8_t config_version,
                FanConfig fan1,
                FanConfig fan2,
                FanConfig fan3,
                FanConfig fan4,
                FanConfig fan5,
                FanConfig fan6,
                SensorConfig tempSupply,
                SensorConfig tempReturn,
                SensorConfig tempCase,
                SensorConfig tempAux1,
                SensorConfig tempAux2);

  int toBytes(byte *bytes, const uint16_t len) const;
  tfcproto_RuntimeConfigV1 toProto() const;

  static RuntimeConfig parse_bytes(const byte bytes[], const uint16_t len);
  static RuntimeConfig from_proto(tfcproto_RuntimeConfigV1 &config);
};


#endif //TFC_RUNTIMECONFIG_H

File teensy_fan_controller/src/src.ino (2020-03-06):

#include <memory>

#include "runtime_config.h"
#include "temp_controller.h"
#include "core.h"

#ifdef USB_RAWHID_EN
#include "hid.h"
#endif

// timers invoke ISR callbacks that toggle these flags, enabling the logic in loop(void):
volatile bool doRPM = false;
volatile bool doADC = false;
volatile bool doPID = false;
volatile bool doHIDSend = false;
bool doLog = false;

// use 500ms timer interrupt to average pulses to RPM (and enable log logic)
IntervalTimer rpmTimer;

// use PERIOD_UPDATE ms timer interrupt to enable ADC read (and PID update)
IntervalTimer adcTimer;

RuntimeConfig config;  // saved in EEPROM (using protobuf / tfcproto_RuntimeConfigV1)

SensorData supplyTemp = SensorData(config.tempSupply, "CWS-T");  // Water Supply Temp
SensorData returnTemp = SensorData(config.tempReturn, "CWR-T");  // Water Return Temp
SensorData caseTemp = SensorData(config.tempCase, "Case-T");
SensorData aux1Temp = SensorData(config.tempAux1, "Aux1-T");
SensorData aux2Temp = SensorData(config.tempAux2, "Aux2-T");
FanData fan1 = FanData(config.fan1, "1");
FanData fan2 = FanData(config.fan2, "2");
FanData fan3 = FanData(config.fan3, "3");
FanData fan4 = FanData(config.fan4, "4");
FanData fan5 = FanData(config.fan5, "5");
FanData fan6 = FanData(config.fan6, "6");

#ifndef DISABLE_EEPROM
byte rbuffer[CONFIG_BYTES];  // EEPROM buffer
#endif
uint8_t logIntervalCnt = 0;

// needed for controller function pointers:
void setup_hardware();
void update_eeprom();

// primary ctrl/TempController
TempController ctrl(config, supplyTemp, returnTemp, caseTemp, aux1Temp, aux2Temp, fan1, fan2, fan3, fan4, fan5, fan6, setup_hardware, update_eeprom);

// HID controller
#ifdef USB_RAWHID_EN
HID hid(ctrl);
#endif


/**
   ISR called from PERIOD_UPDATE ms (100ms) timer (adcTimer).

   Enables do_adc() and do_pid() logic.
*/
void timer_adc_handler()
{
  doADC = true;
  doPID = true;
}

/**
   ISR called from 500ms timer (rpmTimer).

   Enables do_rpm(), and do_log() (every 10 calls).
*/
void timer_rpm_handler()
{
  doRPM = true;
  doHIDSend = true;
}

/*
   Interrupt handlers, bound for each fan RPM signal.
*/

void interrupt_handler1()
{
  fan1.pulse_counter++;
}

void interrupt_handler2()
{
  fan2.pulse_counter++;
}

void interrupt_handler3()
{
  fan3.pulse_counter++;
}

void interrupt_handler4()
{
  fan4.pulse_counter++;
}

void interrupt_handler5()
{
  fan5.pulse_counter++;
}

void interrupt_handler6()
{
  fan6.pulse_counter++;
}

void setup_hardware()
{
  supplyTemp.setupPin();
  returnTemp.setupPin();
  caseTemp.setupPin();
  aux1Temp.setupPin();
  aux2Temp.setupPin();
  fan1.setupPin(interrupt_handler1);
  fan2.setupPin(interrupt_handler2);
  fan3.setupPin(interrupt_handler3);
  fan4.setupPin(interrupt_handler4);
  fan5.setupPin(interrupt_handler5);
  fan6.setupPin(interrupt_handler6);
}

void read_eeprom()
{
#ifndef DISABLE_EEPROM
  memset(rbuffer, '\0', CONFIG_BYTES);
  read_config(rbuffer, CONFIG_BYTES);
  Serial.println("Config read from EEPROM");
  config = RuntimeConfig::parse_bytes(rbuffer, CONFIG_BYTES);
#else
  config = RuntimeConfig();
#endif
}

void update_eeprom()
{
#ifndef DISABLE_EEPROM
  if (config.toBytes(rbuffer, CONFIG_BYTES) == 0) {
    write_config(rbuffer, CONFIG_BYTES);
    Serial.println("Config written to EEPROM");
  }
#else
  Serial.println("Config NOT written to EEPROM");
#endif
}


void setup(void)
{
  Serial.begin(9600);

#ifndef ARDUINO_TEENSY40
  analogReference(EXTERNAL);
#endif
  analogReadResolution(ADC_RESOLUTION);

  read_eeprom();

  // initialize controller (calls setup_hardware())
  ctrl.configChanged(false);

  rpmTimer.begin(timer_rpm_handler, PERIOD_RPM * 1000);
  adcTimer.begin(timer_adc_handler, PERIOD_UPDATE * 1000);
}

/**
   Flush pulse_counter to RPM (2 pulse per revolution, over 0.5s...) for each fan. Invoked once every 500ms.
*/
void do_rpm()
{
  fan1.doRPM();
  fan2.doRPM();
  fan3.doRPM();
  fan4.doRPM();
  fan5.doRPM();
  fan6.doRPM();
}

/**
   Calculate fan PWN % (PID & table), and write PWM outputs. Invoked once every 100ms.
*/
void do_pid()
{
  ctrl.doFanUpdate();
}

/**
   Read ADC signals. Invoked once every 500ms.
*/
void do_adc()
{
  // average NUMSAMPLES of samples, each delayed by READ_DELAY
  uint8_t i;
  for (i = 0; i < NUMSAMPLES; i++) {
    if (supplyTemp.cfg.pin)
      supplyTemp.samples[i] = analogRead(supplyTemp.cfg.pin);
    if (returnTemp.cfg.pin)
      returnTemp.samples[i] = analogRead(returnTemp.cfg.pin);
    if (caseTemp.cfg.pin)
      caseTemp.samples[i] = analogRead(caseTemp.cfg.pin);
    if (aux1Temp.cfg.pin)
      aux1Temp.samples[i] = analogRead(aux1Temp.cfg.pin);
    if (aux2Temp.cfg.pin)
      aux2Temp.samples[i] = analogRead(aux2Temp.cfg.pin);
    delay(READ_DELAY);
  }

  // convert readings to tempC
  supplyTemp.doSample();
  returnTemp.doSample();
  caseTemp.doSample();
  aux1Temp.doSample();
  aux2Temp.doSample();
}

/*
   Macros for do_log().
*/

#define PRINT_RPM(str, lbl, f)\
  { Serial.print("; ");Serial.print(str);Serial.print(lbl);Serial.print(" ");Serial.print(f->rpm); }
#define PRINT_TEMP(str, temp)\
  { Serial.print(str); Serial.print(temp); Serial.print("°C; "); }
#define PRINT_PCT(pct)\
  { Serial.print(pct); Serial.print("%"); }

/**
   Writes data log to (usb raw hid) serial. Invoked once every 500ms.
*/
void do_log()
{
  if (supplyTemp.cfg.pin) {
    PRINT_TEMP("CWS-T ", supplyTemp.val);
  }
  if (returnTemp.cfg.pin) {
    if (supplyTemp.cfg.pin) {
      PRINT_TEMP("DeltaT ", ctrl.getDeltaT());
    }
    else {
      PRINT_TEMP("CWR-T ", returnTemp.val);
    }
  }

  if (caseTemp.cfg.pin) {
    PRINT_TEMP("Case-T ", caseTemp.val);
  }
  if (aux1Temp.cfg.pin) {
    PRINT_TEMP("Aux1-T ", aux1Temp.val);
  }
  if (aux2Temp.cfg.pin) {
    PRINT_TEMP("Aux2-T ", aux2Temp.val);
  }

  // Iterate over the map
  uint8_t i = 0;
  for (const auto &value : ctrl.getControlModes()) {
    if (value.mode == CONTROL_MODE::MODE_OFF)
      break;  // remaining control modes are off

    if (i++ != 0)
      Serial.print("; ");

    Serial.print(" (");
    Serial.print(value.label);
    Serial.print(": ");

    if (value.mode == CONTROL_MODE::MODE_PID) {
      PRINT_TEMP("Setpoint ", value.pidCtrl->getSetpoint());
      PRINT_PCT(value.pct);
    }
    else if (value.mode == CONTROL_MODE::MODE_TBL) {
      PRINT_PCT(value.pct);
    }
    else if (value.mode == CONTROL_MODE::MODE_FIXED) {
      PRINT_PCT(value.pct);
    }

    // loop and print RPM for each fan associated to this control mode
    for (const auto &fan : value.fans) {
      if (fan != nullptr) {
        if (fan->cfg.pinRPM)
          PRINT_RPM("RPM", fan->lbl, fan);
      }
      else {
        break;
      }
    }
    Serial.print(")");
  }
  Serial.println();
}


#ifdef USB_RAWHID_EN
/**
   Reads command from HID raw.
*/
void do_hid_recv()
{
  hid.recv();
}

/**
   Transmits HID raw data packet(s) (which packet sent depends on HID state). Invoked once every 500ms.
*/
void do_hid_send()
{
  if (hid.send() < 0) {
    Serial.println("Unable to transmit packet");
  }
}
#endif


void loop(void)
{
  if (doADC) {
    doADC = false;
    do_adc();
  }

  if (doPID) {
    doPID = false;
    do_pid();
  }

#ifdef USB_RAWHID_EN
  do_hid_recv();

  if (doHIDSend) {
    doHIDSend = false;
    do_hid_send();
  }
#endif

  if (doRPM) {
    doRPM = false;
    do_rpm();

    // print log every 5 seconds
    if (++logIntervalCnt >= 10) {
      logIntervalCnt = 0;
      doLog = true;
    }
  }
  if (doLog) {
    doLog = false;
    do_log();
  }
}

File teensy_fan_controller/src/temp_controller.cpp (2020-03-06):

//
// Created by jd on 11/26/2019.
//

#include "temp_controller.h"


TempController::PIDController::PIDController(const RuntimeConfig::PIDConfig &pidCfg)
    : pidCfg(pidCfg), setpoint(pidCfg.setpoint), in(0), pct(0),
      pid(&in, &pct, &setpoint, pidCfg.gain_p, pidCfg.gain_i, pidCfg.gain_d, PID::REVERSE)
{
  // configure PID
  pid.SetSampleTime(SAMPLE_PERIOD);
  if (setpoint >= pidCfg.setpoint_max)
    pid.SetOutputLimits(pidCfg.pwm_percent_min, pidCfg.pwm_percent_max2);
  else
    pid.SetOutputLimits(pidCfg.pwm_percent_min, pidCfg.pwm_percent_max1);
  pid.SetMode(PID::AUTOMATIC);  // start PID
}

uint8_t TempController::PIDController::sample(const float &sample, const SensorData &caseTemp)
{
  in = sample;
  pid.Compute();  // Calculate Fan % using PID controller

  if (pidCfg.adaptive_sp) {
    // adapt set-point when fan% below or above thresholds
    bool changed = false;
    bool withinCaseTempLimit = true;
    if (pct <= pidCfg.adaptive_sp_step_down.pct) {
      lastSincePercentsAboveLimit = 0;
      if (lastSincePercentsBelowLimit == 0)
        lastSincePercentsBelowLimit = millis();
      if (millis() - lastSincePercentsBelowLimit > pidCfg.adaptive_sp_step_down.delay * 1000) {
        // (temp has been below limit for the required duration)
        if (pidCfg.adaptive_sp_check_case_temp && caseTemp.cfg.pin) {
          // require (case_temp <= setpoint - <delta>) to step down setpoint
          if (caseTemp.val > setpoint - pidCfg.adaptive_sp_step_down.case_temp_delta)
            withinCaseTempLimit = false;
        }
        if (withinCaseTempLimit && setpoint - pidCfg.adaptive_sp_step_size >= pidCfg.setpoint_min) {
          // decrement setpoint by step size
          setpoint -= pidCfg.adaptive_sp_step_size;
          lastSincePercentsBelowLimit = 0;
          changed = true;
        }
      }
    }
    else if (pct >= pidCfg.adaptive_sp_step_up.pct) {
      lastSincePercentsBelowLimit = 0;
      if (lastSincePercentsAboveLimit == 0)
        lastSincePercentsAboveLimit = millis();
      if (millis() - lastSincePercentsAboveLimit > pidCfg.adaptive_sp_step_up.delay * 1000) {
        // (temp has been above limit for the required duration)
        if (pidCfg.adaptive_sp_check_case_temp && caseTemp.cfg.pin) {
          // require (case_temp >= setpoint - <delta>) to step up setpoint
          if (caseTemp.val < setpoint - pidCfg.adaptive_sp_step_up.case_temp_delta)
            withinCaseTempLimit = false;
        }
        if (withinCaseTempLimit && setpoint + pidCfg.adaptive_sp_step_size <= pidCfg.setpoint_max) {
          // increment setpoint by step size
          setpoint += pidCfg.adaptive_sp_step_size;
          lastSincePercentsAboveLimit = 0;
          changed = true;
        }
      }
    }
    else {
      lastSincePercentsAboveLimit = 0;
      lastSincePercentsBelowLimit = 0;
    }
    if (changed || !withinCaseTempLimit) {
      // update fan % limit
      if (!withinCaseTempLimit || setpoint >= pidCfg.setpoint_max)
        pid.SetOutputLimits(pidCfg.pwm_percent_min, pidCfg.pwm_percent_max2);
      else
        pid.SetOutputLimits(pidCfg.pwm_percent_min, pidCfg.pwm_percent_max1);
    }
  }
  return pct;
}

const float &TempController::PIDController::getSetpoint() const
{
  return setpoint;
}


TempController::ControlData::ControlData()
    : sample(nullptr),
      pidCtrl(nullptr),
      fans{{nullptr, nullptr, nullptr, nullptr, nullptr, nullptr}},
      mode(CONTROL_MODE::MODE_OFF), source(static_cast<uint8_t>(CONTROL_SOURCE::SENSOR_WATER_SUPPLY_TEMP)),
      label("")
{}

TempController::ControlData::~ControlData()
{
  if (pidCtrl != nullptr) {
    delete pidCtrl;
    pidCtrl = nullptr;
  }
}

void TempController::ControlData::resetPIDCtrl()
{
  if (this->pidCtrl != nullptr) {
    delete this->pidCtrl;
    this->pidCtrl = nullptr;
  }
}

void TempController::ControlData::reset()
{
  this->resetPIDCtrl();

  // turn off all fans
  for (auto &fan : fans) {
    if (fan != nullptr)
      fan->writePWM(0, false);
    else
      break;
  }

  this->sample = nullptr;
  this->pidCtrl = nullptr;
  this->fans = {{nullptr, nullptr, nullptr, nullptr, nullptr, nullptr}};
  this->mode = CONTROL_MODE::MODE_OFF;
  this->source = static_cast<uint8_t>(CONTROL_SOURCE::SENSOR_WATER_SUPPLY_TEMP);
  this->pct = 0;
  this->fanNo = 0;
  this->label = "";
}

void TempController::ControlData::setPctTable(float *const sample, const CONTROL_MODE mode, const CONTROL_SOURCE source, const uint8_t fanNo, const String &label)
{
  this->resetPIDCtrl();

  this->sample = sample;
  this->pidCtrl = nullptr;
  this->fans = {{nullptr, nullptr, nullptr, nullptr, nullptr, nullptr}};
  this->mode = mode;
  this->source = static_cast<uint8_t>(source);
  this->pct = 0;
  this->fanNo = fanNo;
  this->label = label;
}

void TempController::ControlData::setPID(SensorData *const pidSensor, const CONTROL_MODE mode, const CONTROL_SOURCE source, const uint8_t fanNo, const String &label)
{
  this->resetPIDCtrl();

  this->sample = &pidSensor->val;
  this->pidCtrl = new PIDController(pidSensor->cfg.pid);
  this->fans = {{nullptr, nullptr, nullptr, nullptr, nullptr, nullptr}};
  this->mode = mode;
  this->source = static_cast<uint8_t>(source);
  this->pct = 0;
  this->fanNo = fanNo;
  this->label = label;
}

void TempController::ControlData::setFixed(float *const sample, const CONTROL_MODE mode, const uint8_t source, const uint8_t pct, const uint8_t fanNo, const String &label)
{
  this->resetPIDCtrl();

  this->sample = sample;
  this->pidCtrl = nullptr;
  this->fans = {{nullptr, nullptr, nullptr, nullptr, nullptr, nullptr}};
  this->mode = mode;
  this->source = source;
  this->pct = pct;
  this->fanNo = fanNo;
  this->label = label;
}

uint8_t TempController::ControlData::doPID(const SensorData &caseTemp)
{
  if (pidCtrl != nullptr)
    return pct = static_cast<uint8_t>(round(pidCtrl->sample(*sample, caseTemp)));
  else
    return pct = 0;
}

uint8_t TempController::ControlData::doTbl(const auto &tempPctTbl)
{
  // Calculates Fan % using only tempPercentTable
  const float &reading = *sample;
  float lastTemp = 0,
        curTemp;
  uint8_t lastPct = 0,
          curPct, i;
  for (i = 0; i < FAN_TBL_SIZE; i++) {
    curTemp = tempPctTbl[i][0];
    curPct = tempPctTbl[i][1];
    if (reading <= curTemp) {  // use this entry
      if (i > 0) {  // calc % between lastEntry and this entry
        return pct = (1 - ((curTemp - reading) / (curTemp - lastTemp))) * (curPct - lastPct) + lastPct;
      }
      else if (curPct >= 100) {
        return pct = 100;
      }
      else {  // use % in table
        return pct = curPct;
      }
    }
    lastPct = curPct;
    lastTemp = curTemp;
  }
  return pct = curPct;
}

uint8_t TempController::ControlData::doFixed()
{
  return pct;  // pct is set after construct for fixed control
}
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

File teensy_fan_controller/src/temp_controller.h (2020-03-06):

//
// Created by jd on 11/26/2019.
//

#ifndef TFC_TEMP_CONTROLLER_H
#define TFC_TEMP_CONTROLLER_H

#include <array>
#include <PID_v1.h>
#include "runtime_config.h"
#include "core.h"


/**
   A single TempController instance is used by the main application to calculate fan PWM %.
*/
class TempController {
  public:
    typedef PIDt<float, float, float> PID;

    struct ControlData;

    /**
       Each temp sensor may operate a PID controller through an instance of this controller.
    */
    class PIDController {
      private:
        const RuntimeConfig::PIDConfig &pidCfg;
        float setpoint;
        float in;
        float pct;
        PID pid;

        unsigned long lastSincePercentsBelowLimit = 0;
        unsigned long lastSincePercentsAboveLimit = 0;
        bool lastPercentsAboveLimit = false;
        bool lastPercentsBelowLimit = false;

      public:
        PIDController(const RuntimeConfig::PIDConfig &pidCfg);

        uint8_t sample(const float &sample, const SensorData &caseTemp);

        const float &getSetpoint() const;
    };

    /**
       Used to group a set of fans to a unique control strategy.
    */
    struct ControlData {
      float *sample;
      PIDController *pidCtrl;
      std::array<FanData *, FAN_CNT> fans;
      CONTROL_MODE mode;
      uint8_t source;  //CONTROL_SOURCE (or fixed fan %)
      uint8_t pct = 0;
      uint8_t fanNo = 0;  // the first fan associated w/ this control data
      String label;

      ControlData();
      ~ControlData();

      void resetPIDCtrl();
      void setPctTable(float *const sample, const CONTROL_MODE mode, const CONTROL_SOURCE source, const uint8_t fanNo, const String &label);  // %-tbl constructor
      void setPID(SensorData *const pidSensor, const CONTROL_MODE mode, const CONTROL_SOURCE source, const uint8_t fanNo, const String &label);  // PID constructor
      void setFixed(float *const sample, const CONTROL_MODE mode, const uint8_t source, const uint8_t pct, const uint8_t fanNo, const String &label);  // fixed-% constructor
      void reset();

      // delete copy assignment
      ControlData(const ControlData &that) = delete;
      ControlData &operator=(const ControlData &that) = delete;

      uint8_t doPID(const SensorData &caseTemp);
      uint8_t doTbl(const auto &tempPctTbl);
      uint8_t doFixed();

      uint8_t getFanCount() const;
    };


  public:
    static const uint16_t SAMPLE_PERIOD = PERIOD_UPDATE;

    RuntimeConfig &config;

    SensorData &supplyTemp;  // Water Supply Temp
    SensorData &returnTemp;  // Water Return Temp
    SensorData &caseTemp;
    SensorData &aux1Temp;
    SensorData &aux2Temp;

    TempController(RuntimeConfig &config,
                   SensorData &supplyTemp, SensorData &returnTemp, SensorData &caseTemp, SensorData &aux1Temp, SensorData &aux2Temp,
                   FanData &fan1, FanData &fan2, FanData &fan3, FanData &fan4, FanData &fan5, FanData &fan6,
                   void (*const setupHardware)(),
                   void (*const saveConfig)());

    void configChanged(bool doSave = true);
    void doFanUpdate();
    void resetControlModes();

    const float &getDeltaT() const;
    float getPIDSupplyTempSetpoint() const;
    float getPIDAux1TempSetpoint() const;
    const FanData &getFan(uint8_t i) const;
    const std::array<ControlData, FAN_CNT> &getControlModes() const;


  private:
    const std::array<FanData *const, FAN_CNT> fans;
    std::array<ControlData, FAN_CNT> controlModes;

    float deltaT;  // returnTemp - supplyTemp (0 if no returnTemp sensor)

    ControlData &findOrCreateControlMode(CONTROL_MODE mode, uint8_t source, uint8_t i);

    void (*const setupHardware)();  // callback to update pin muxing after config changes
    void (*const saveConfig)();  // callback to save config to EEPROM after config changes
};


#endif //TFC_TEMP_CONTROLLER_H

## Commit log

2019-12-18 TFC-0 Initial commit (teensy_fan_controller/) TFC-0 Initial commit (README.md) TFC-0 Initial commit (Hardware/Schmart Board/) TFC-0 Initial commit (firmware/TODO)
2019-12-29 TFC-0 increase default PID step-up case limit to 1.8degC
2019-12-29 TFC-0 track Qt5-HIDAPI + TFC-ui git projects
2019-12-30 TFC-0 track latest UI project
2020-01-07 TFC-1 multiple PID + tbl configs TFC-1 HID_CONFIG/HID_DOWNLOAD more config chunks TFC-1 track latest ui
2020-01-11 proj-2 replace std::map w/ fixed size array (avoid linking libstdc) proj-2 CONTROL_MODE MODE_OFF for unused ControlData proj-2 used fixed allocation for controllers and ControlData proj-2 add DISABLE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
    [core.cpp, core.h, hid.cpp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]
2020-01-11 proj-2 HID qa + track latest ui
2020-01-11 proj-2 disable EEPROM (at compile time) if device EEPROM is not large enough proj-2 static_assert CONFIG_BYTES is large enough for __RuntimeConfig_v1
2020-01-11 proj-2 TableConfig float datatype for % and temperature steps proj-2 HID dynamic config chunk count proj-2 update CONFIG_KEYs proj-2 track latest UI
2020-01-11 TFC-0 set pin states to default when longer in use TFC-0 README update
2020-01-12 TFC-1 track latest ui
2020-01-16 #3 readme updates #3 readme add PID Usage Example w/ charts
2020-01-17 #1 data payload include aux1Temp, aux2Temp, deltaT #1 qa %-table bugfix #1 qa report correct fan RPM #1 track latest UI
    [hid.cpp, temp_controller.cpp, temp_controller.h]
2020-01-25 #1 track latest UI
2020-02-22 #5 Simple001 PCB schematic, board, and related project files
    [parts.csv, simple001.brd, simple001.sch]
2020-02-28 #4 support ARDUINO_TEENSY40 constant from later teensy cores release
2020-02-28 #4 add teensy_fan_controller Makefile for building project w/o Arduino Studio
2020-02-28 #4 track latest ui_qt5
2020-03-03 #4 firmware Makefile allow setting TEENSY from CLI
2020-03-03 #4 breadboard hardware support files
    [router cooling exp.fzz]
2020-03-03 #4 firmware support Arduino Studio (move teensy_fan_controller.ino to src.ino)
2020-03-03 #4 reference forked PID library, track latest changes
2020-03-03 #4 firmware use PID library as PID<float, float, float>
2020-03-04 #4 track latest UI
2020-03-04 #4 TempController cleanup: static SAMPLE_PERIOD, typedef PID, const deltaT() and const func ptrs; track latest PID
2020-03-05 #1 fixed control bugfix/save fan off bugfix
    [core.cpp, core.h, runtime_config.cpp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]
2020-03-05 #4 reduce LC memory footprint, reduce string concats, track latest UI
2020-03-06 #1 #4 report %-table PWM % in log, mstrthealias/TFC-ui#2 improve present values, track latest ui
2020-03-07 mstrthealias/TFC-ui#2 track latest ui, attribute flaticon in README
2020-03-08 #4 track latest UI; GIMP assets for UI icon
2020-04-25 #8 hardware move simple001 to simple002
    [parts.csv, simple001.brd, simple001.sch]
2020-04-25 #8 hardware rename simple001 files to simple002
    [simple002.brd, simple002.sch]
2020-04-25 #8 hardware correct simple001 board mount hole positions
    [simple002.brd]
2020-04-25 #8 hardware simple002 correct fan6 PWM to support Teensy 3.2, 3.5, 3.6, 4.0
    [simple002.brd, simple002.sch]
2020-04-25 #8 hardware restore published simple001 files
    [parts.csv]
2020-04-25 #8 hardware move EAGLE to parent directory
    [simple002.brd, simple002.sch]
